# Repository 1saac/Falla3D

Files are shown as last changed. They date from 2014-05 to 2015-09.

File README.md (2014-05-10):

Fa)(a 3d !

IT:
Stampante 3D Open Source con scorrimento assi X Y su guide a levitazione magnetica, modulare (estrusione tutti i filamenti 3mm e 1.75) e scalabile!

EN:
OpenSource 3D Printer with a magnetic levitation system for the bearings of the X and Y axes. The printer is also modular (it can extrude all 3mm and 1.75 mm filaments) and scalable!

FR:
Une imprimante 3D OpenSource avec un système de levitation magnétique pour le mouvement des axes X et Y. La machine est aussi modularie (extrudent tous les filaments de 3 mm et 1.75 mm) et extensible!

ES:
Una impresora 3D OpenSource con escurrimiento a levitaciòn magnètica de los ejes X y Y, modular (puede extrudir todos los filamentos de 3mm y 1.75 mm) y de tamaño escalar!

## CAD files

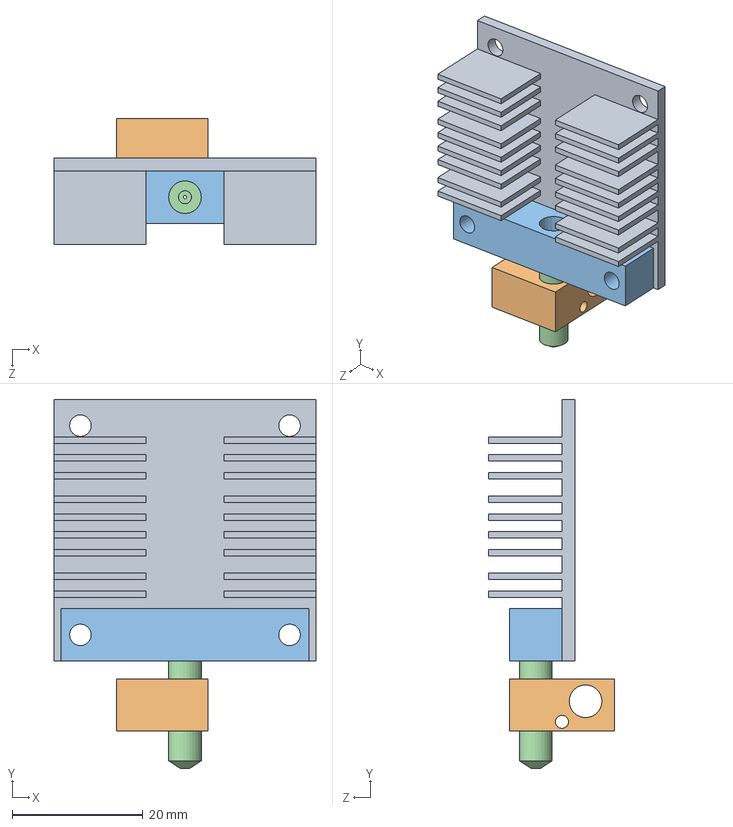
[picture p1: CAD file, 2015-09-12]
source/3/extruer.SLDASM
40.0 x 56.4 x 19.2 mm
heat_sink
nozzle_cube
nozzle_05

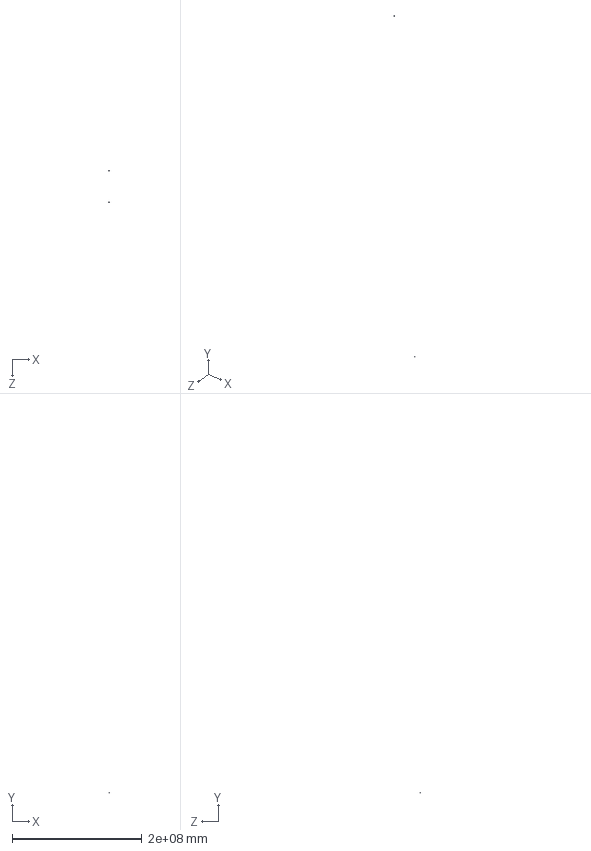
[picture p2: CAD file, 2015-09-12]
source/3/pla.SLDASM
327.3 x 592448256.0 x 48036592.0 mm
05 Profilato
NK_02_17_01_260
NW_02_17_1 x 2
magnet_50x3x5
bearings_623 x 4
bottom_
top_
socket button head cap screw_am x 10
socket head cap screw_am x 4
prevailing torque hex nut_am x 4
Mirrorbottom_
Mirrorbearings_623 x 4
Mirrortop_
Guide_NS-01-27_slider
L_profile x 2
Guide_NS-01-27

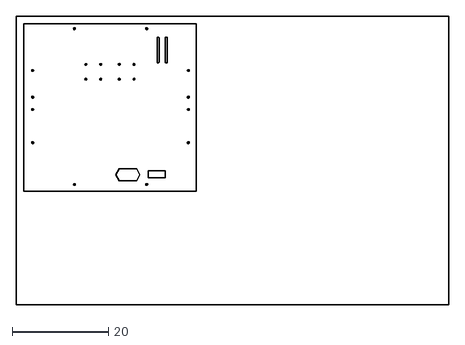
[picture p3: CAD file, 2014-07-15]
dxf/Vers_1.95/rear.dxf
90.0 x 60.0

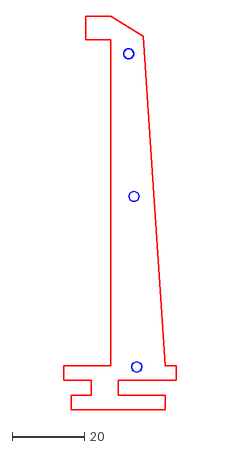
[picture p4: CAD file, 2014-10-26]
dxf/Vers_2.0/optional/4x_spoolHolder.dxf
31.0 x 108.7

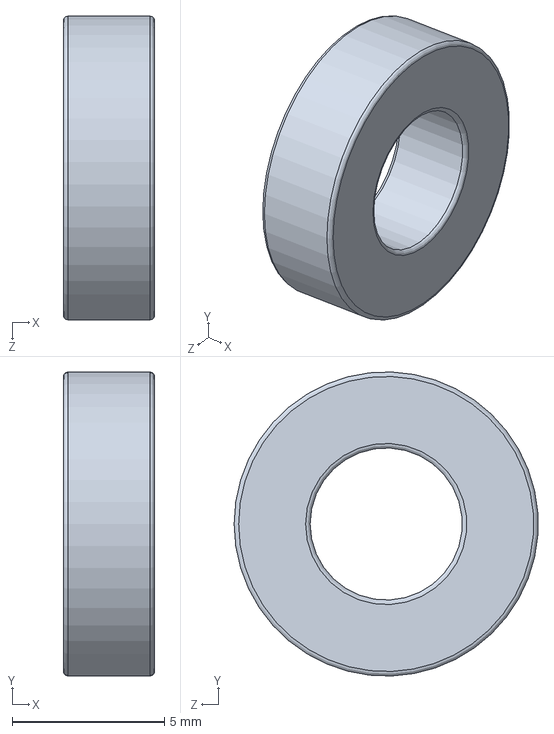
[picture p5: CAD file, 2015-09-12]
source/3/bearing_mr105_0/bearing_mr105_0.SLDPRT
3.00 x 9.99 x 9.99 mm

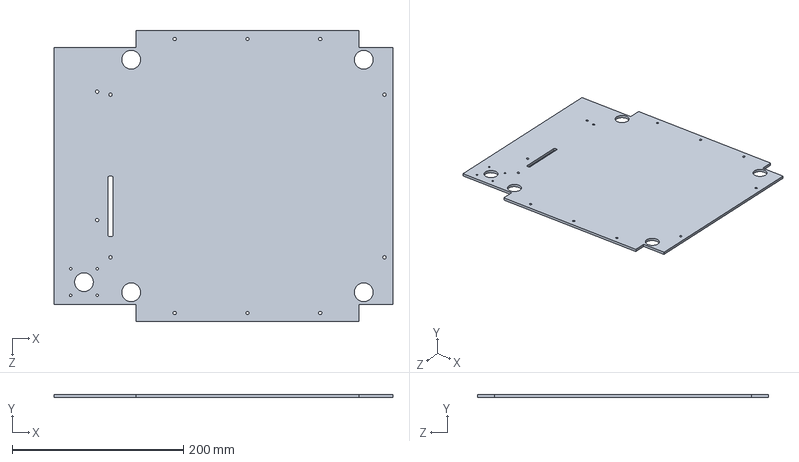
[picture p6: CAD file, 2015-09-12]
source/3/falla_nexttop.SLDPRT
396.0 x 4.00 x 340.0 mm

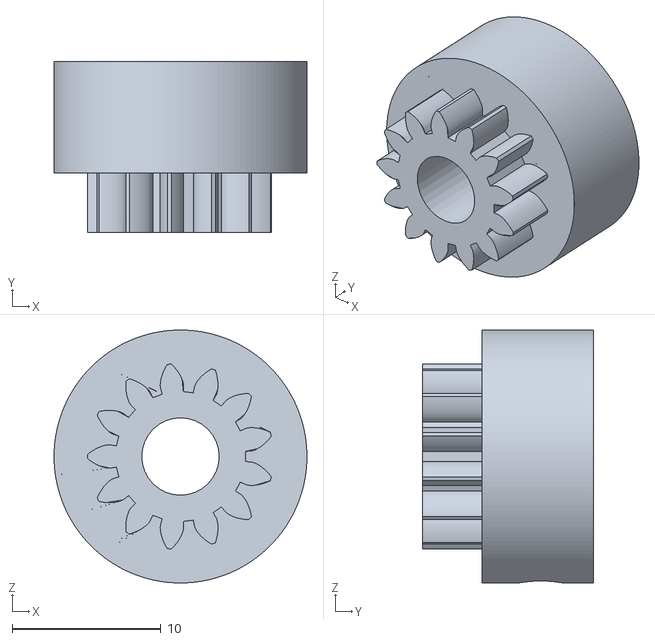
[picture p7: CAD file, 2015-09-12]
stl/ver_2.0/ABS/3mmExtr/Small_gear.stl
17.0 x 11.5 x 17.0

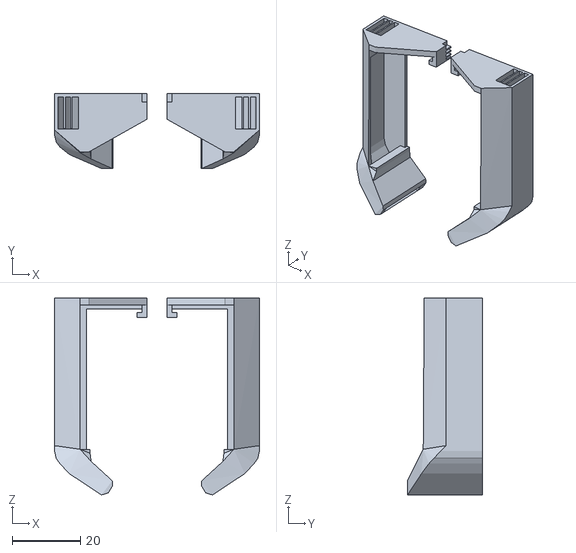
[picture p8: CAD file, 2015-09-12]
stl/ver_2.0/ABS/extruderFAN.stl
59.9 x 21.9 x 57.5

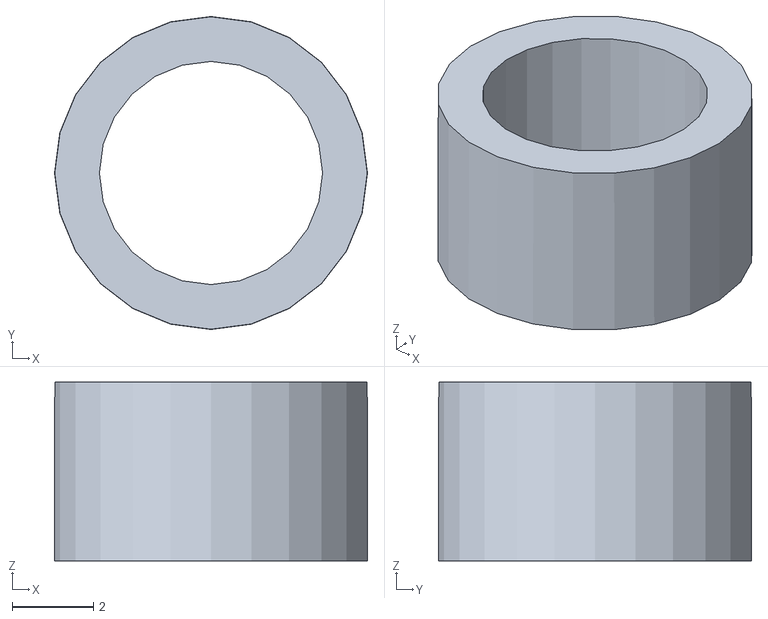
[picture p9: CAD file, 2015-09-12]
stl/ver_2.0/nylon/4X_Bearing_ilder/abs2.stl
7.71 x 7.71 x 4.41

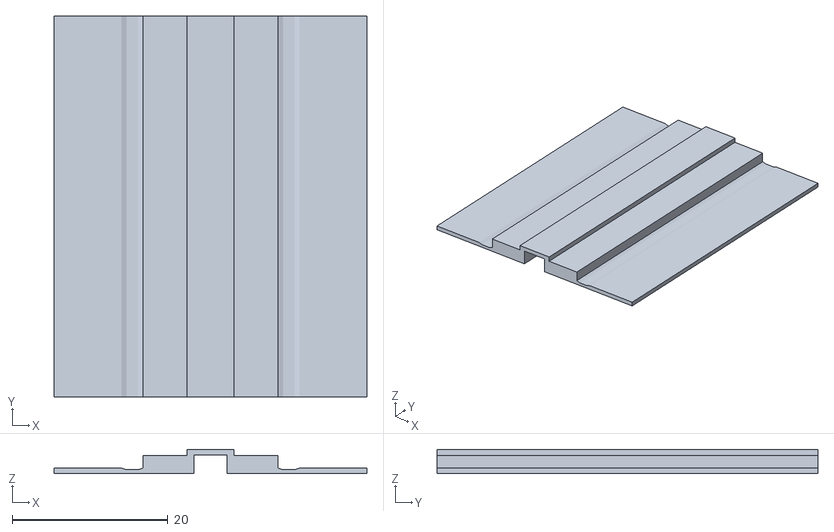
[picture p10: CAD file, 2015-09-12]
stl/ver_2.0/nylon/x6_nylon_slider_4D.stl
40.2 x 49.0 x 3.10

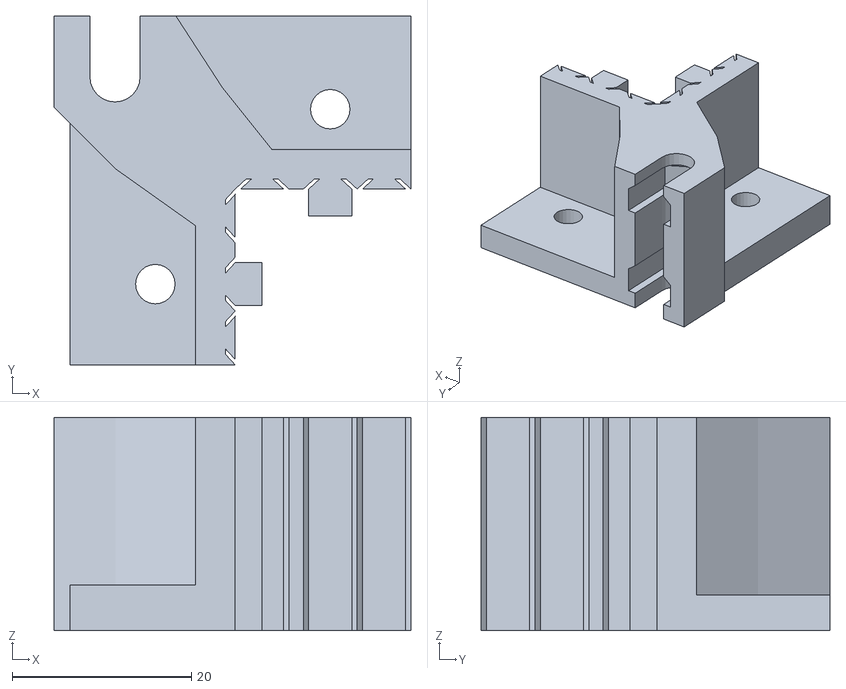
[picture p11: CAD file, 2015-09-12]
stl/ver_2.0/nylon/Z_slider/ABS_core.stl
39.8 x 38.9 x 23.8

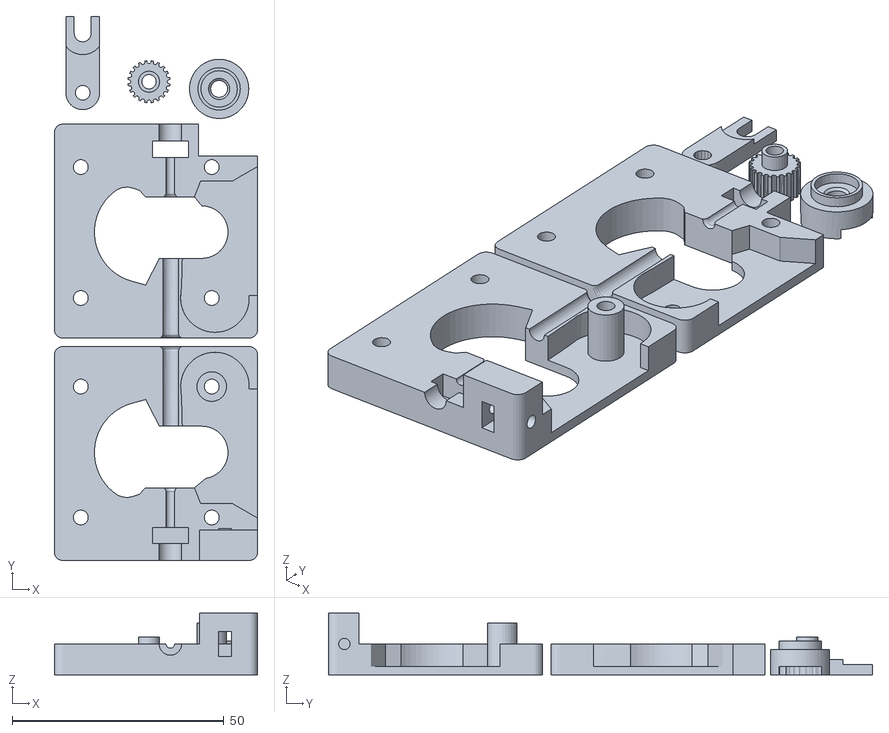
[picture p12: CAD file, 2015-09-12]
stl/ver_2.0/PLAorABS/extruder_nema17/part1.stl
48.0 x 128.4 x 14.6

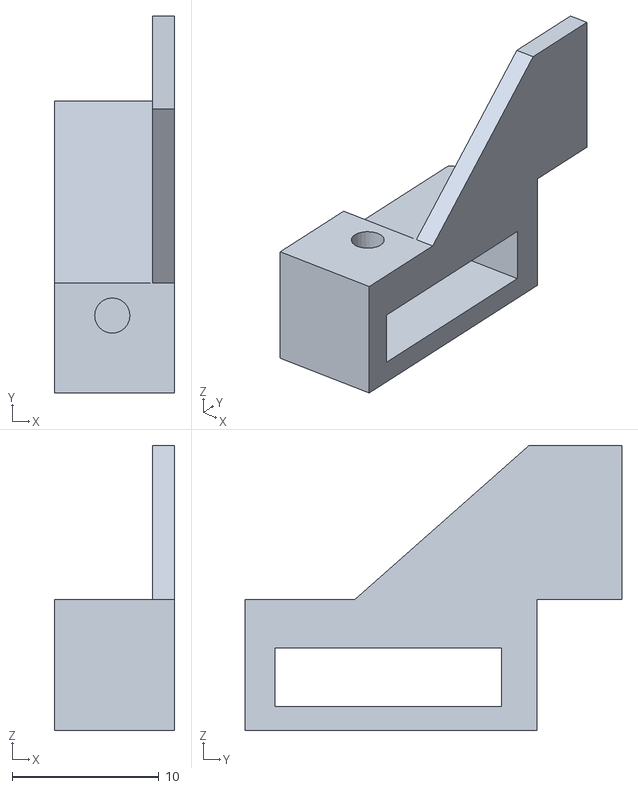
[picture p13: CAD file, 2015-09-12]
stl/ver_2.0/PLAorABS/flag.stl
8.20 x 25.7 x 19.4

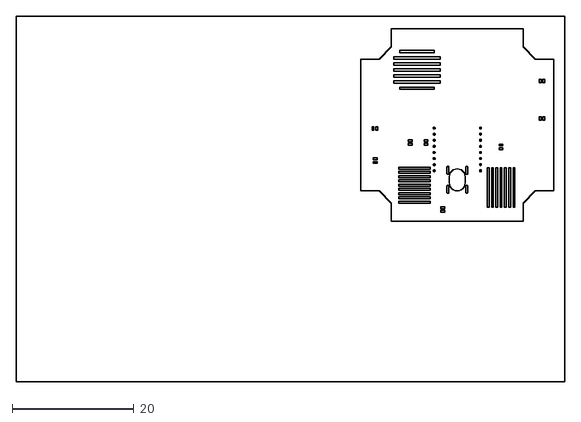
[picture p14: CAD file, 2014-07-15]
dxf/Vers_1.95/underplate.dxf
90.0 x 60.0

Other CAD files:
dxf/Vers_1.95/cork/nema14.dwg
dxf/Vers_2.0/AngleMotor_2x_Kerf_009_nema17.dwg
dxf/Vers_2.0/Angle_6x_Kerf_009.dxf
dxf/Vers_2.0/optional/Front.dxf
dxf/Vers_1.95/enclosure_left_right.dxf
dxf/Vers_1.95/plate.dxf
dxf/Vers_1.95/topFront_frame1x.dxf
dxf/Vers_1.95/trasparentFront_frame.dxf
dxf/Vers_2.0/Back_Kerf_009.dxf
dxf/Vers_2.0/CoverFront_Kerf_009.dxf
dxf/Vers_2.0/CoverTop_Kerf_009.dxf
dxf/Vers_2.0/Plate_Kerf_009.dxf
dxf/Vers_2.0/Underplate_Kerf_009.dxf
dxf/Vers_2.0/cork_nema14.dxf
dxf/Vers_2.0/optional/x2_Lateral.dxf
source/3/05 Profilato.SLDPRT
source/3/243 Profilato.SLDPRT
source/3/50 PowerSupply.SLDPRT
source/3/50x40X2.SLDPRT
source/3/B18.2.4.1M - Hex nut, Style 1, M8 x 1.25 --D-N.sldprt
source/3/Electronic_back.SLDPRT
source/3/Electronics_cover.SLDPRT
source/3/GT2_20tooth.SLDPRT
source/3/Guide_NS-01-27-200.SLDPRT
source/3/Guide_NS-01-27-40.SLDPRT
source/3/Guide_NS-01-27.SLDPRT
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

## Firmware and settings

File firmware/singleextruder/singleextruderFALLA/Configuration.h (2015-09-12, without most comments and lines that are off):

#define CONFIGURATION_H
#define STRING_VERSION_CONFIG_H __DATE__ " " __TIME__ // build date and time
#define STRING_CONFIG_H_AUTHOR "(none, default config)" //Who made the changes.
#define SERIAL_PORT 0
#define BAUDRATE 115200
#define MOTHERBOARD 33
#define POWER_SUPPLY 1
#define TEMP_SENSOR_0 7
#define TEMP_SENSOR_1 0
#define TEMP_SENSOR_2 0
#define TEMP_SENSOR_BED 1
#define TEMP_RESIDENCY_TIME 10	// (seconds)
#define TEMP_HYSTERESIS 3       // (degC) range of +/- temperatures considered "close" to the target one
#define TEMP_WINDOW     1       // (degC) Window around target to start the recidency timer x degC early.
#define HEATER_0_MINTEMP 5
#define HEATER_1_MINTEMP 5
#define HEATER_2_MINTEMP 5
#define BED_MINTEMP 5
#define HEATER_0_MAXTEMP 275
#define HEATER_1_MAXTEMP 275
#define HEATER_2_MAXTEMP 275
#define BED_MAXTEMP 150
#define PIDTEMP
#define BANG_MAX 256 // limits current to nozzle while in bang-bang mode; 256=full current
#define PID_MAX 256 // limits current to nozzle while PID is active (see PID_FUNCTIONAL_RANGE below); 256=full current
  #define PID_FUNCTIONAL_RANGE 10 // If the temperature difference between the target temperature and the actual temperature
  #define PID_INTEGRAL_DRIVE_MAX 255  //limit for the integral term
  #define K1 0.95 //smoothing factor withing the PID
  #define PID_dT ((16.0 * 8.0)/(F_CPU / 64.0 / 256.0)) //sampling period of the temperature routine
    #define  DEFAULT_Kp 15.58
    #define  DEFAULT_Ki 0.98
    #define  DEFAULT_Kd 61.76
#define BED_LIMIT_SWITCHING //*
#define MAX_BED_POWER 256 // limits duty cycle to bed; 256=full current
#define PREVENT_DANGEROUS_EXTRUDE
#define PREVENT_LENGTHY_EXTRUDE
#define EXTRUDE_MINTEMP 20
#define EXTRUDE_MAXLENGTH (X_MAX_LENGTH+Y_MAX_LENGTH) //prevent extrusion of very large distances.
  #define ENDSTOPPULLUP_XMAX
  #define ENDSTOPPULLUP_YMAX
  #define ENDSTOPPULLUP_XMIN
  #define ENDSTOPPULLUP_YMIN
const bool X_ENDSTOPS_INVERTING = true; // set to true to invert the logic of the endstops.
const bool Y_ENDSTOPS_INVERTING = true; // set to true to invert the logic of the endstops.
const bool Z_ENDSTOPS_INVERTING = false; // set to true to invert the logic of the endstops.
#define X_ENABLE_ON 0
#define Y_ENABLE_ON 0
#define Z_ENABLE_ON 0
#define E_ENABLE_ON 0 // For all extruders
#define DISABLE_X false
#define DISABLE_Y false
#define DISABLE_Z false
#define DISABLE_E false // For all extruders
#define INVERT_X_DIR false     // for Mendel set to false, for Orca set to true
#define INVERT_Y_DIR false    // for Mendel set to true, for Orca set to false
#define INVERT_Z_DIR false     // for Mendel set to false, for Orca set to true
#define INVERT_E0_DIR true   // for direct drive extruder v9 set to true, for geared extruder set to false
#define INVERT_E1_DIR false    // for direct drive extruder v9 set to true, for geared extruder set to false
#define INVERT_E2_DIR false   // for direct drive extruder v9 set to true, for geared extruder set to false
#define X_HOME_DIR -1
#define Y_HOME_DIR -1
#define Z_HOME_DIR -1
#define min_software_endstops false //If true, axis won't move to coordinates less than HOME_POS.
#define max_software_endstops true  //If true, axis won't move to coordinates greater than the defined lengths below.
#define X_MAX_POS 205
#define X_MIN_POS 0
#define Y_MAX_POS 205
#define Y_MIN_POS 0
#define Z_MAX_POS 200
#define Z_MIN_POS 0
#define X_MAX_LENGTH (X_MAX_POS - X_MIN_POS)
#define Y_MAX_LENGTH (Y_MAX_POS - Y_MIN_POS)
#define Z_MAX_LENGTH (Z_MAX_POS - Z_MIN_POS)
#define MANUAL_X_HOME_POS 0
#define MANUAL_Y_HOME_POS 0
#define MANUAL_Z_HOME_POS 0
#define NUM_AXIS 4 // The axis order in all axis related arrays is X, Y, Z, E
#define HOMING_FEEDRATE {50*60, 50*60, 80, 0}  // set the homing speeds (mm/min)
#define DEFAULT_AXIS_STEPS_PER_UNIT   {81.0000, 81.0000, 4045, 90.1}  //3985- 18 thoot on motor  4045- 20 thoot on motor
#define DEFAULT_MAX_FEEDRATE          {400, 400, 2, 60}    // (mm/sec)
#define DEFAULT_MAX_ACCELERATION      {1800,1800,40,10000}    // X, Y, Z, E maximum start speed for accelerated moves. E default values are good for skeinforge 40+, for older versions raise them a lot.
#define DEFAULT_ACCELERATION          1800    // X, Y, Z and E max acceleration in mm/s^2 for printing moves
#define DEFAULT_RETRACT_ACCELERATION  1800   // X, Y, Z and E max acceleration in mm/s^2 for r retracts
#define DEFAULT_XYJERK                15.0    // (mm/sec)
#define DEFAULT_ZJERK                 0.4     // (mm/sec)
#define DEFAULT_EJERK                 5.0    // (mm/sec)
#define EEPROM_CHITCHAT
#define REPRAP_DISCOUNT_SMART_CONTROLLER
 #define ULTIPANEL
 #define NEWPANEL
#define PLA_PREHEAT_HOTEND_TEMP 180
#define PLA_PREHEAT_HPB_TEMP 70
#define PLA_PREHEAT_FAN_SPEED 255		// Insert Value between 0 and 255
#define ABS_PREHEAT_HOTEND_TEMP 240
#define ABS_PREHEAT_HPB_TEMP 100
#define ABS_PREHEAT_FAN_SPEED 255		// Insert Value between 0 and 255
  #define SDSUPPORT
  #define ULTRA_LCD
		#define LCD_WIDTH 20
		#define LCD_HEIGHT 4
#include "Configuration_adv.h"
#include "thermistortables.h"

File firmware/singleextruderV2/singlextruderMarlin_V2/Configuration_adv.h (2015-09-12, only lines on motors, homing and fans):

#define CONTROLLERFAN_PIN -1 //Pin used for the fan to cool controller (-1 to disable)
#define EXTRUDER_0_AUTO_FAN_PIN   -1
#define EXTRUDER_1_AUTO_FAN_PIN   -1
#define EXTRUDER_2_AUTO_FAN_PIN   -1
#define ENDSTOPS_ONLY_FOR_HOMING // If defined the endstops will only be used for homing
#define X_HOME_RETRACT_MM 5
#define Y_HOME_RETRACT_MM 5
#define Z_HOME_RETRACT_MM 2
#define MICROSTEP1 LOW,LOW
#define MICROSTEP2 HIGH,LOW
#define MICROSTEP4 LOW,HIGH
#define MICROSTEP8 HIGH,HIGH
#define MICROSTEP16 HIGH,HIGH
#define MICROSTEP_MODES {16,16,16,16,16} // [1,2,4,8,16]
#define DIGIPOT_MOTOR_CURRENT {135,135,135,135,135} // Values 0-255 (RAMBO 135 = ~0.75A, 185 = ~1A)
#define DIGIPOT_I2C_MOTOR_CURRENTS {1.0, 1.0, 1.0, 1.0, 1.0, 1.0, 1.0, 1.0}

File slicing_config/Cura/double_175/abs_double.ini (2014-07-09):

[profile]
layer_height = 0.30
wall_thickness = 1.5
retraction_enable = True
solid_layer_thickness = 0.6
fill_density = 0
nozzle_size = 0.5
print_speed = 65
print_temperature = 213
print_temperature2 = 213
print_temperature3 = 0
print_temperature4 = 0
print_bed_temperature = 90
support = None
platform_adhesion = None
support_dual_extrusion = Both
wipe_tower = True
wipe_tower_volume = 15
ooze_shield = False
filament_diameter = 1.75
filament_diameter2 = 1.75
filament_diameter3 = 0
filament_diameter4 = 0
filament_flow = 100.0
retraction_speed = 45.0
retraction_amount = 5.8
retraction_dual_amount = 16
retraction_min_travel = 0.2
retraction_combing = True
retraction_minimal_extrusion = 0.2
retraction_hop = 0.0
bottom_thickness = 0.0
object_sink = 0.0
overlap_dual = 0.15
travel_speed = 100.0
bottom_layer_speed = 30
infill_speed = 0.0
inset0_speed = 0.0
insetx_speed = 0.0
cool_min_layer_time = 12
fan_enabled = True
skirt_line_count = 4
skirt_gap = 3.0
skirt_minimal_length = 150.0
fan_full_height = 0.5
fan_speed = 60
fan_speed_max = 100
cool_min_feedrate = 8
cool_head_lift = False
solid_top = True
solid_bottom = True
fill_overlap = 25
support_type = Grid
support_angle = 0
support_fill_rate = 35
support_xy_distance = 0.7
support_z_distance = 0.15
spiralize = False
brim_line_count = 22
raft_margin = 5
raft_line_spacing = 1.3
raft_base_thickness = 0.30
raft_base_linewidth = 0.25
raft_interface_thickness = 0.20
raft_interface_linewidth = 0.20
fix_horrible_union_all_type_a = False
fix_horrible_union_all_type_b = False
fix_horrible_use_open_bits = False
fix_horrible_extensive_stitching = False
plugin_config = (lp1
	.
object_center_x = -1
object_center_y = -1

[alterations]
start.gcode = ;Sliced at: {day} {date} {time}
	;Basic settings: Layer height: {layer_height} Walls: {wall_thickness} Fill: {fill_density}
	;Print time: {print_time}
	;Filament used: {filament_amount}m {filament_weight}g
	;Filament cost: {filament_cost}
	;M190 S90 ;Uncomment to add your own bed temperature line
	;M109 S{print_temperature} ;Uncomment to add your own temperature line
	G92 E89.90
	G21        ;metric values
	G90        ;absolute positioning
	M107       ;start with the fan off
	G28 X0 Y0  ;move X/Y to min endstops
	G28 Z0     ;move Z to min endstops
	G1 Z15.0 F{travel_speed} ;move the platform down 15mm
	G92 E0                  ;zero the extruded length
	G1 F200 E3              ;extrude 3mm of feed stock
	G92 E0                  ;zero the extruded length again
	G1 F{travel_speed}
	;Put printing message on LCD screen
	M117 Printing...
end.gcode = ;End GCode
	M104 S0                     ;extruder heater off
	M140 S0                     ;heated bed heater off (if you have it)
	G91                                    ;relative positioning
	G1 E-1 F300                            ;retract the filament a bit before lifting the nozzle, to release some of the pressure
	G1 Z+0.5 E-5 X-20 Y-20 F{travel_speed} ;move Z up a bit and retract filament even more
	G28 X0 Y0                              ;move X/Y to min endstops, so the head is out of the way
	M84                         ;steppers off
	G90                         ;absolute positioning
start2.gcode = ;Sliced at: {day} {date} {time}
	;Basic settings: Layer height: {layer_height} Walls: {wall_thickness} Fill: {fill_density}
	;Print time: {print_time}
	;Filament used: {filament_amount}m {filament_weight}g
	;Filament cost: {filament_cost}
	;M190 S{print_bed_temperature} ;Uncomment to add your own bed temperature line
	;M104 S{print_temperature} ;Uncomment to add your own temperature line
	;M109 T1 S{print_temperature2} ;Uncomment to add your own temperature line
	;M109 T0 S{print_temperature} ;Uncomment to add your own temperature line
	G21        ;metric values
	G90        ;absolute positioning
	M107       ;start with the fan off
	G28 X0 Y0  ;move X/Y to min endstops
	G28 Z0     ;move Z to min endstops
	G1 Z15.0 F{travel_speed} ;move the platform down 15mm
	T1                      ;Switch to the 2nd extruder
	G92 E0                  ;zero the extruded length
	G1 F200 E10             ;extrude 10mm of feed stock
	G92 E0                  ;zero the extruded length again
	G1 F200 E-{retraction_dual_amount}
	T0                      ;Switch to the first extruder
	G92 E0                  ;zero the extruded length
	G1 F200 E10             ;extrude 10mm of feed stock
	G92 E0                  ;zero the extruded length again
	G1 F{travel_speed}
	;Put printing message on LCD screen
	M117 Printing...
end2.gcode = ;End GCode
	M104 T0 S0                     ;extruder heater off
	M104 T1 S0                     ;extruder heater off
	M140 S0                     ;heated bed heater off (if you have it)
	G91                                    ;relative positioning
	G1 E-1 F300                            ;retract the filament a bit before lifting the nozzle, to release some of the pressure
	G1 Z+0.5 E-5 X-20 Y-20 F{travel_speed} ;move Z up a bit and retract filament even more
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

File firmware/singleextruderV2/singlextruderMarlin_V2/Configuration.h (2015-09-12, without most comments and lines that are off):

#define CONFIGURATION_H
#define STRING_VERSION_CONFIG_H __DATE__ " " __TIME__ // build date and time
#define STRING_CONFIG_H_AUTHOR "(none, default config)" // Who made the changes.
#define SERIAL_PORT 0
#define BAUDRATE 250000
#define MOTHERBOARD 33
#define EXTRUDERS 1
#define POWER_SUPPLY 1
#define TEMP_SENSOR_0 7
#define TEMP_SENSOR_1 7
#define TEMP_SENSOR_2 0
#define TEMP_SENSOR_BED 1
#define MAX_REDUNDANT_TEMP_SENSOR_DIFF 10
#define TEMP_RESIDENCY_TIME 3  // (seconds)
#define TEMP_HYSTERESIS 3       // (degC) range of +/- temperatures considered "close" to the target one
#define TEMP_WINDOW     1       // (degC) Window around target to start the residency timer x degC early.
#define HEATER_0_MINTEMP 5
#define HEATER_1_MINTEMP 5
#define HEATER_2_MINTEMP 5
#define BED_MINTEMP 5
#define HEATER_0_MAXTEMP 275
#define HEATER_1_MAXTEMP 275
#define HEATER_2_MAXTEMP 275
#define BED_MAXTEMP 150
#define PIDTEMP
#define BANG_MAX 255 // limits current to nozzle while in bang-bang mode; 255=full current
#define PID_MAX 255 // limits current to nozzle while PID is active (see PID_FUNCTIONAL_RANGE below); 255=full current
  #define PID_FUNCTIONAL_RANGE 10 // If the temperature difference between the target temperature and the actual temperature
  #define PID_INTEGRAL_DRIVE_MAX 255  //limit for the integral term
  #define K1 0.95 //smoothing factor within the PID
  #define PID_dT ((OVERSAMPLENR * 10.0)/(F_CPU / 64.0 / 256.0)) //sampling period of the temperature routine
    #define  DEFAULT_Kp 15.58
    #define  DEFAULT_Ki 0.98
    #define  DEFAULT_Kd 61.76
#define PIDTEMPBED
#define BED_LIMIT_SWITCHING
#define MAX_BED_POWER 255 // limits duty cycle to bed; 255=full current
    #define  DEFAULT_bedKp 381.36//97.1
    #define  DEFAULT_bedKi 54.77//1.41
    #define  DEFAULT_bedKd 633.90//1675.16
#define PREVENT_DANGEROUS_EXTRUDE
#define PREVENT_LENGTHY_EXTRUDE
#define EXTRUDE_MINTEMP 20
#define EXTRUDE_MAXLENGTH (X_MAX_LENGTH+Y_MAX_LENGTH) //prevent extrusion of very large distances.
#define ENDSTOPPULLUPS // Comment this out (using // at the start of the line) to disable the endstop pullup resistors
  #define ENDSTOPPULLUP_XMIN
  #define ENDSTOPPULLUP_YMIN
const bool X_MIN_ENDSTOP_INVERTING = true; // set to true to invert the logic of the endstop.
const bool Y_MIN_ENDSTOP_INVERTING = true; // set to true to invert the logic of the endstop.
const bool Z_MIN_ENDSTOP_INVERTING = false; // set to true to invert the logic of the endstop.
const bool X_MAX_ENDSTOP_INVERTING = true; // set to true to invert the logic of the endstop.
const bool Y_MAX_ENDSTOP_INVERTING = true; // set to true to invert the logic of the endstop.
const bool Z_MAX_ENDSTOP_INVERTING = false; // set to true to invert the logic of the endstop.
#if defined(COREXY) && !defined(DISABLE_MAX_ENDSTOPS)
  #define DISABLE_MAX_ENDSTOPS
#endif
#define X_ENABLE_ON 0
#define Y_ENABLE_ON 0
#define Z_ENABLE_ON 0
#define E_ENABLE_ON 0 // For all extruders
#define DISABLE_X false
#define DISABLE_Y false
#define DISABLE_Z false
#define DISABLE_E false // For all extruders
#define DISABLE_INACTIVE_EXTRUDER true //disable only inactive extruders and keep active extruder enabled
#define INVERT_X_DIR false    // for Mendel set to false, for Orca set to true
#define INVERT_Y_DIR false    // for Mendel set to true, for Orca set to false
#define INVERT_Z_DIR false     // for Mendel set to false, for Orca set to true
#define INVERT_E0_DIR true   // for direct drive extruder v9 set to true, for geared extruder set to false
#define INVERT_E1_DIR false    // for direct drive extruder v9 set to true, for geared extruder set to false
#define INVERT_E2_DIR false   // for direct drive extruder v9 set to true, for geared extruder set to false
#define X_HOME_DIR -1
#define Y_HOME_DIR -1
#define Z_HOME_DIR -1
#define min_software_endstops false // If true, axis won't move to coordinates less than HOME_POS.
#define max_software_endstops true  // If true, axis won't move to coordinates greater than the defined lengths below.
#define X_MAX_POS 205
#define X_MIN_POS 0
#define Y_MAX_POS 205
#define Y_MIN_POS 0
#define Z_MAX_POS 200
#define Z_MIN_POS 0
#define X_MAX_LENGTH (X_MAX_POS - X_MIN_POS)
#define Y_MAX_LENGTH (Y_MAX_POS - Y_MIN_POS)
#define Z_MAX_LENGTH (Z_MAX_POS - Z_MIN_POS)
#define Z_PROBE_REPEATABILITY_TEST  // If not commented out, Z-Probe Repeatability test will be included if Auto Bed Leveling is Enabled.
#define MANUAL_X_HOME_POS 0
#define MANUAL_Y_HOME_POS 0
#define MANUAL_Z_HOME_POS 0
#define NUM_AXIS 4 // The axis order in all axis related arrays is X, Y, Z, E
#define HOMING_FEEDRATE {50*60, 50*60, 4*60, 0}  // set the homing speeds (mm/min)
#define DEFAULT_AXIS_STEPS_PER_UNIT   {81.0000, 81.0000, 4045, 90.1}  // default steps per unit for Ultimaker
#define DEFAULT_MAX_FEEDRATE          {400, 400, 5, 60}    // (mm/sec){400, 400, 2, 60}
#define DEFAULT_MAX_ACCELERATION      {1800,1800,40,10000}    // X, Y, Z, E maximum start speed for accelerated moves. E default values are good for Skeinforge 40+, for older versions raise them a lot.
#define DEFAULT_ACCELERATION          1800    // X, Y, Z and E max acceleration in mm/s^2 for printing moves
#define DEFAULT_RETRACT_ACCELERATION  1800   // X, Y, Z and E max acceleration in mm/s^2 for retracts
#define DEFAULT_XYJERK                15.0    // (mm/sec)
#define DEFAULT_ZJERK                 1     // (mm/sec)
#define DEFAULT_EJERK                 5.0    // (mm/sec)
#define CUSTOM_M_CODES
  #define CUSTOM_M_CODE_SET_Z_PROBE_OFFSET 851
  #define Z_PROBE_OFFSET_RANGE_MIN -15
  #define Z_PROBE_OFFSET_RANGE_MAX -5
#define EEPROM_CHITCHAT
#define PLA_PREHEAT_HOTEND_TEMP 180
#define PLA_PREHEAT_HPB_TEMP 70
#define PLA_PREHEAT_FAN_SPEED 255   // Insert Value between 0 and 255
#define ABS_PREHEAT_HOTEND_TEMP 240
#define ABS_PREHEAT_HPB_TEMP 90
#define ABS_PREHEAT_FAN_SPEED 255   // Insert Value between 0 and 255
#define REPRAP_DISCOUNT_SMART_CONTROLLER
 #define ULTIPANEL
 #define NEWPANEL
  #define SDSUPPORT
  #define ULTRA_LCD
    #define LCD_WIDTH 20
    #define LCD_HEIGHT 4
#define SOFT_PWM_SCALE 0
#define FILAMENT_SENSOR_EXTRUDER_NUM	0  //The number of the extruder that has the filament sensor (0,1,2)
#define MEASUREMENT_DELAY_CM			14  //measurement delay in cm.  This is the distance from filament sensor to middle of barrel
#define DEFAULT_NOMINAL_FILAMENT_DIA  3.0  //Enter the diameter (in mm) of the filament generally used (3.0 mm or 1.75 mm) - this is then used in the slicer software.  Used for sensor reading validation
#define MEASURED_UPPER_LIMIT          3.30  //upper limit factor used for sensor reading validation in mm
#define MEASURED_LOWER_LIMIT          1.90  //lower limit factor for sensor reading validation in mm
#define MAX_MEASUREMENT_DELAY			20  //delay buffer size in bytes (1 byte = 1cm)- limits maximum measurement delay allowable (must be larger than MEASUREMENT_DELAY_CM  and lower number saves RAM)
#define DEFAULT_MEASURED_FILAMENT_DIA  DEFAULT_NOMINAL_FILAMENT_DIA  //set measured to nominal initially
#include "Configuration_adv.h"
#include "thermistortables.h"

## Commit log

2014-05-10 Fa)(a 3D !
    First release!
    [2020handle.stl, Configuration.h, Configuration_adv.h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]
2014-05-11 add DXF Fa)(a 3D!
    [enclosure_left.dxf, enclosure_rear.dxf, enclosure_right.dxf]
2014-05-11 final version 1.74
    [Configuration.h, Configuration_adv.h, FoldaRap2_z-scissor.dxf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]
2014-05-13 bom folder
    add txt bom list
2014-05-15 modify some bearings
2014-07-09 slicer_setting - new DWG - STL file still updating
    [Configuration.h, Configuration_adv.h, EXT_nema17.stl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]
2014-07-09 new nylon 2 version
    test the new version of magnetic guide external ABS-PLA internal
    nylon.. (inside nylon2 folder)
    [x_y_nylon2_slider.stl, x_y_nylon2_slider_ABS-PLA.stl]
2014-07-15 add xy slider version 2
    composite slider nylon+abs/pla version
    [x_y_nylon2_slider_ABS-PLA.stl]
2014-07-15 dxf file
    dxf file
    [plate.dxf, rear.dxf, topFront_frame1x.dxf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]
2014-07-17 spool holder repaired mesh
    spool holder repaired mesh sorry.
    [spool_holder_2x.stl]
2014-08-01 firmware
    Option 20 tooth 18 tooth on Z motor ( on the bars always 20 tooth)
    [Configuration.h]
2014-08-01 Slicing config
    Update for “easy” better resolution
2014-08-01 update source 1.91
    version 1.91
    - implementation of new magnet guide 2.0
    - Minor Fix
2014-08-01 Add Nylon/ABS 1.5 and 2.0 XY magnet GUIDE
    Add Nylon/ABS 1.5 and 2.0 XY magnet GUIDE
    [NEWx_ABS.stl, NEWy_ABS.stl, x_y_nylon2_slider.stl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]
2014-09-03 Spool and head fan add and 1.95 relase
    added 2 spool one of andrea design, and for use the M5 bars, add head
    fan for 2 30x30 fan for the very small print, (useful for 0.3 nozzle
    very small print)
    [Configuration.h, Logo_led.stl, NEWx_ABS.stl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]
2014-10-26 add vers 2.0
    New version 2.0 Falla3d
    - mini hotend
    - powerful magnets
    - all power supply and electronics all in the back
    - ….
    [4_Yspacer.stl, 4x_spoolHolder.dxf, AngleMotor_2x_Kerf_009.dxf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]
2015-09-12 add 2.1 and 3.0 prev
    add minor issue on 2.1 ver and the new core xy 3.0 prev .
    [05 Profilato.SLDPRT, 243 Profilato.SLDPRT, 4x_Z_slider.stl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]
2015-09-12 3.0_ next top
    add linear cut for heated bed cable
    [falla_nextElectronics_cover.SLDPRT, falla_nexttop.SLDPRT]
